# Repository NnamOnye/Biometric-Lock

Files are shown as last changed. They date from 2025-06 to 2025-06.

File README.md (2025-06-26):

ESP-IDF APP
Created by: Nnam Onye
====================

# This is a biometric lock utilizing PIN, and a Finger Print Scanning module.
# This project is already optimized to a certain degree, it can already ask for pin/finger input on first start up + setup
# Has memory to store user pin and finger check and authenticate using memory.
# It can be expanded to save up to as many finger prints and passwords the engineer/designer/user wants.
# The PCB is designed using the same concept as one of my other projects, "keypadPCB" but with additions for the bolt lock,etc..
# I designed the hardware using KiCAD an ECAD Software

# Eclispe Download --> https://eclipseide.org/
# KiCAD Download --> https://www.kicad.org/download/

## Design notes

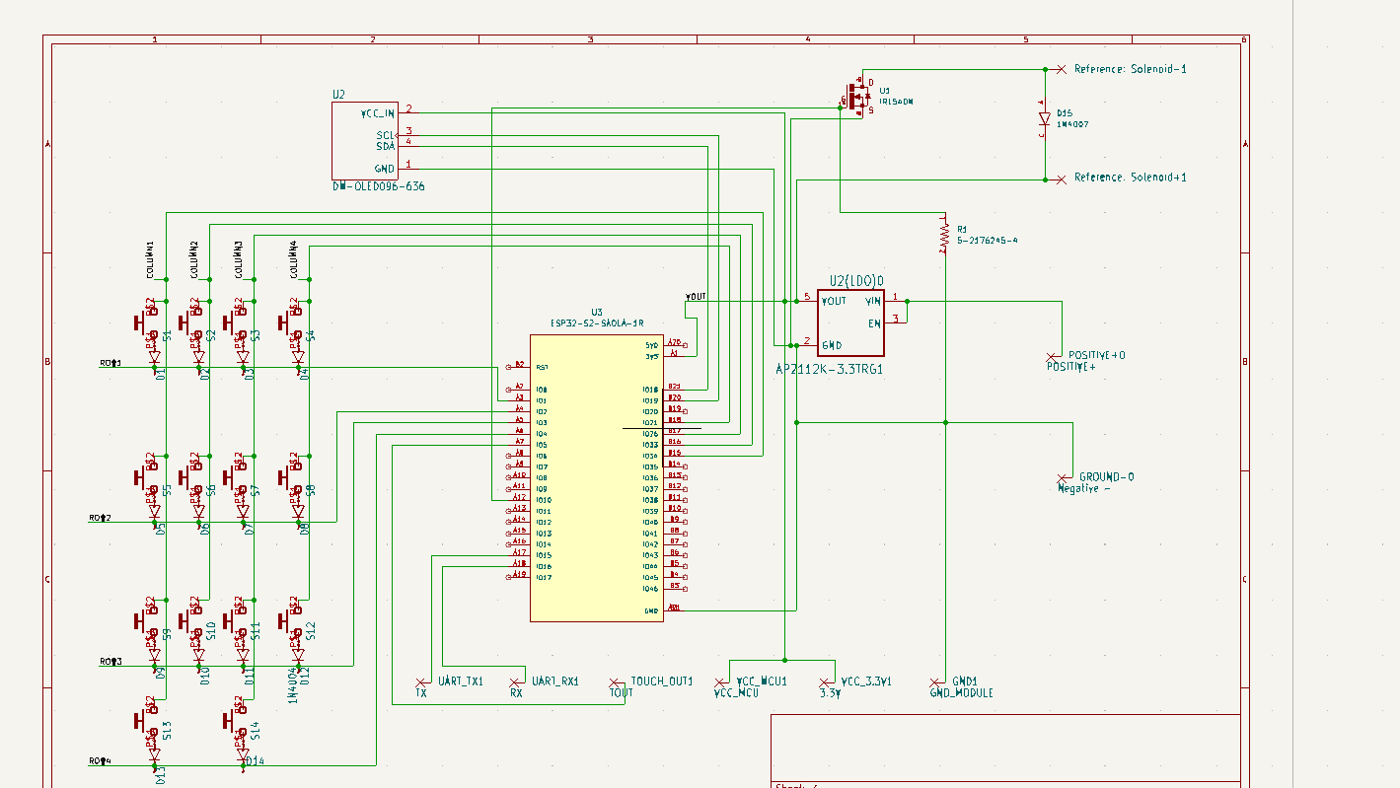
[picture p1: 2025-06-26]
PCB DESIGN/Schematic screenshot.png

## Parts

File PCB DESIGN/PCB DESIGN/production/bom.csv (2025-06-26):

Designator | Footprint | Quantity | Value | LCSC Part #
D1, D10, D11, D12, D13, D14, D2, D3, D4, D5, D6, D7, D8, D9 | DO41-10_210 | 14 | 1N4004
D15 | DIOAD1060W80L520D270 | 1 | 1N4007
GND1 | SMD2,54-5,08_412 | 1 | GND_MODULE
GROUND-0 | SMD2,54-5,08_412 | 1 | Negative -
POSITIVE+0 | SMD2,54-5,08_412 | 1 | POSITIVE+
R1 | RESC3115X65N | 1 | 5-2176245-4
S1, S10, S11, S12, S13, S14, S2, S3, S4, S5, S6, S7, S8, S9 | CHERRY_MX1A-11NN_SWITCH | 14 | MX1A-11NN
SOLENOID+1 | SMD2,54-5,08_412 | 1 | Solenoid+1
SOLENOID-1 | SMD2,54-5,08_412 | 1 | Solenoid-1
TOUCH_OUT1 | SMD2,54-5,08_412 | 1 | TOUT
U1 | TO220V | 1 | IRL540N
U2 | MODULE_DM-OLED096-636 | 1 | DM-OLED096-636
U2(LDO)0 | SOT95P285X140-5N | 1 | AP2112K-3.3TRG1
U3 | XCVR_ESP32-S2-SAOLA-1R | 1 | ESP32-S2-SAOLA-1R
UART_RX1 | SMD2,54-5,08_412 | 1 | RX
UART_TX1 | SMD2,54-5,08_412 | 1 | TX
VCC_3.3V1 | SMD2,54-5,08_412 | 1 | 3.3V
VCC_MCU1 | SMD2,54-5,08_412 | 1 | VCC_MCU

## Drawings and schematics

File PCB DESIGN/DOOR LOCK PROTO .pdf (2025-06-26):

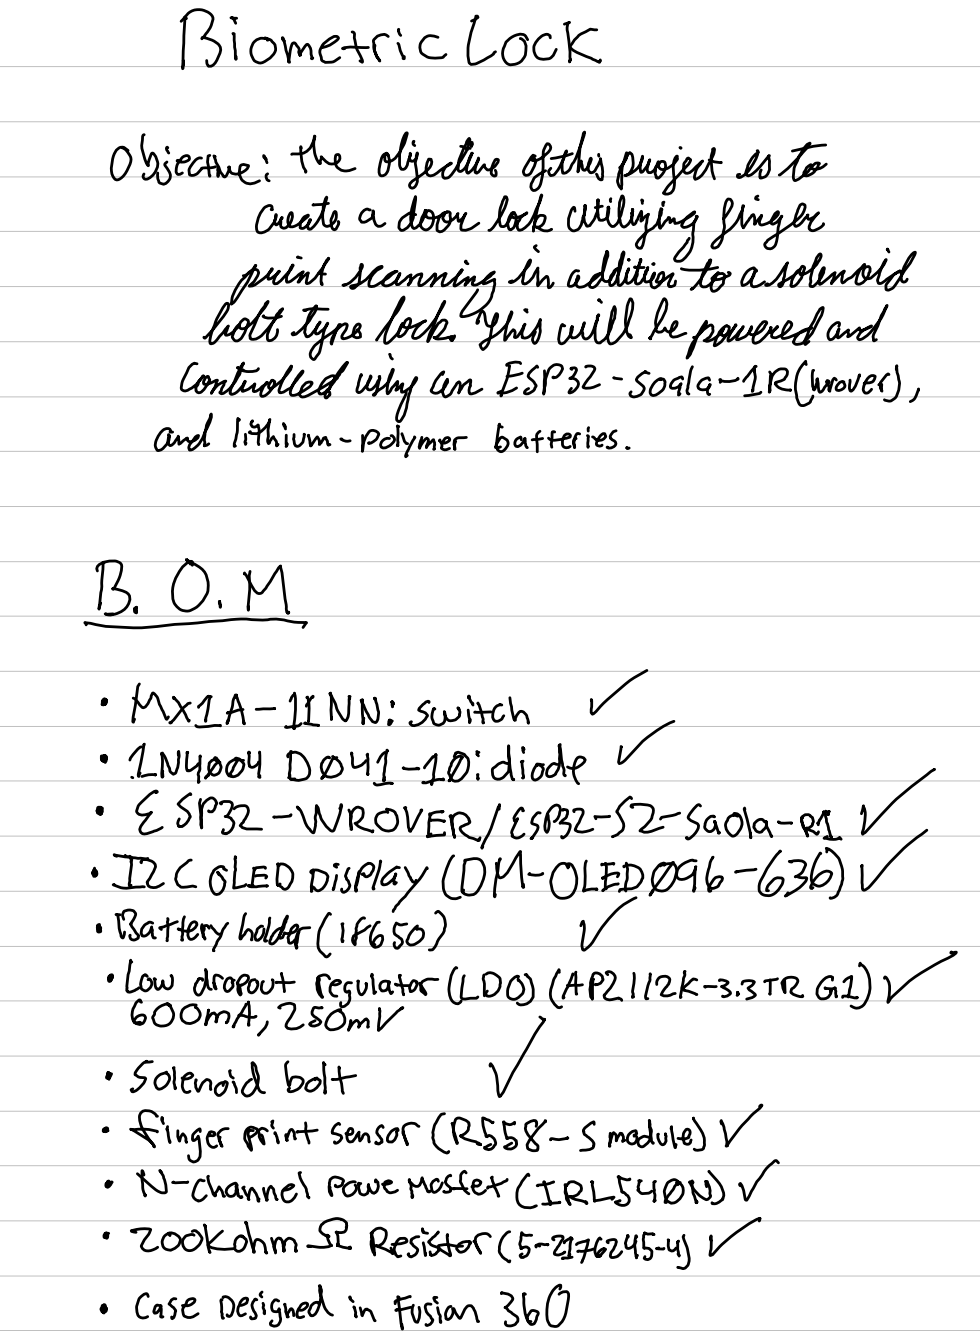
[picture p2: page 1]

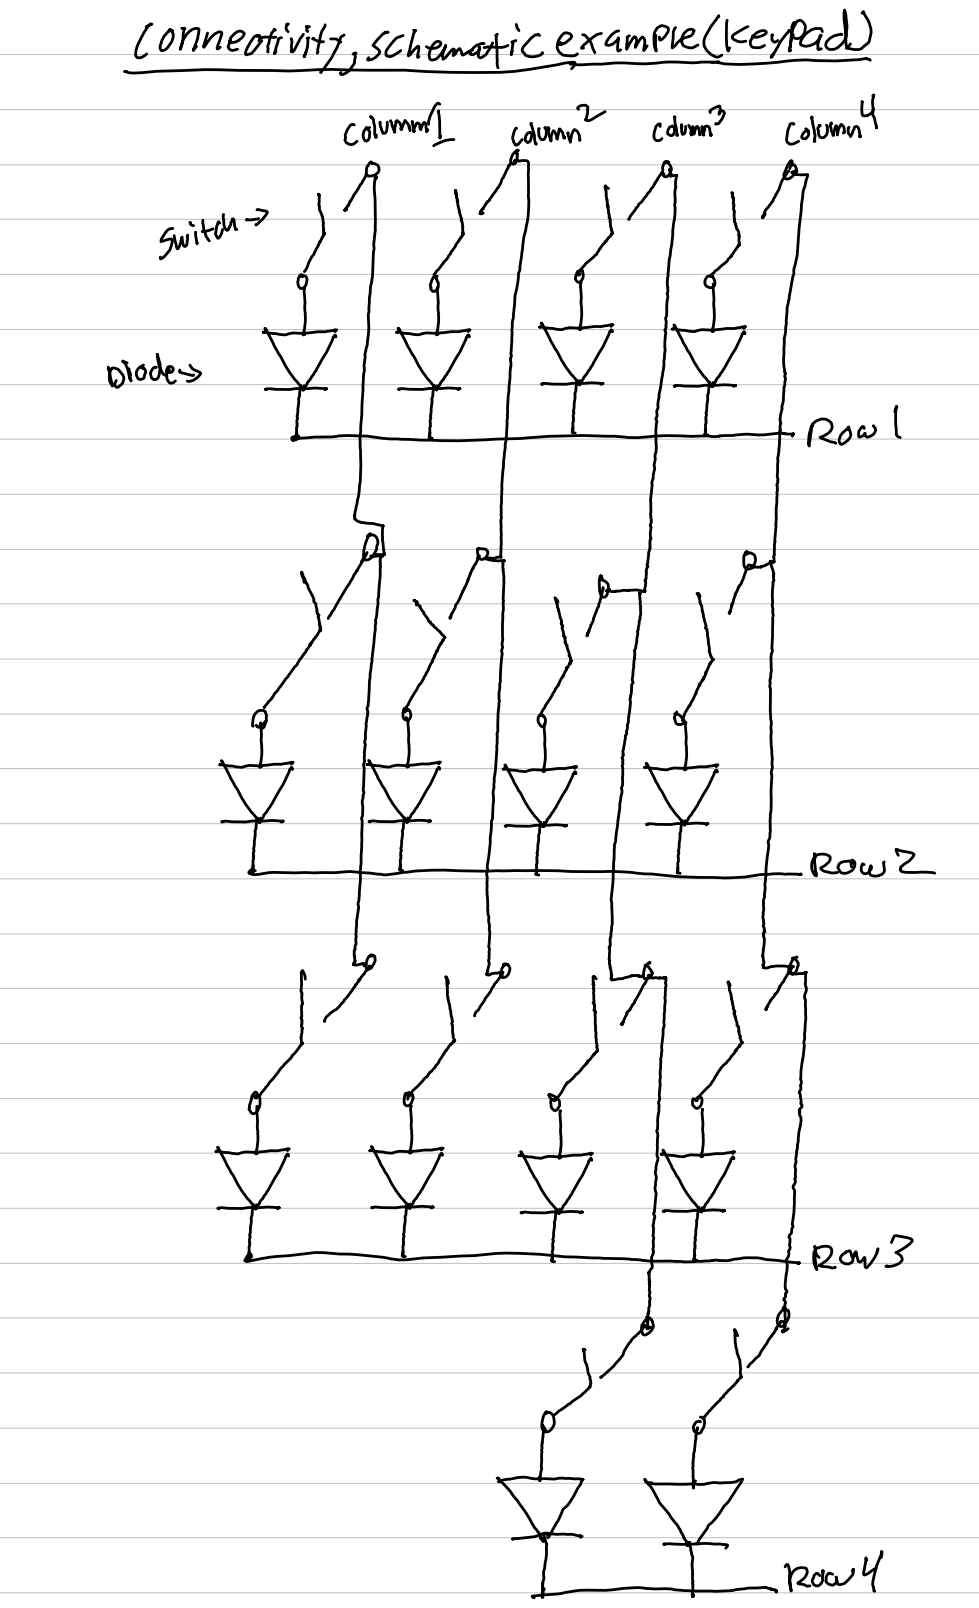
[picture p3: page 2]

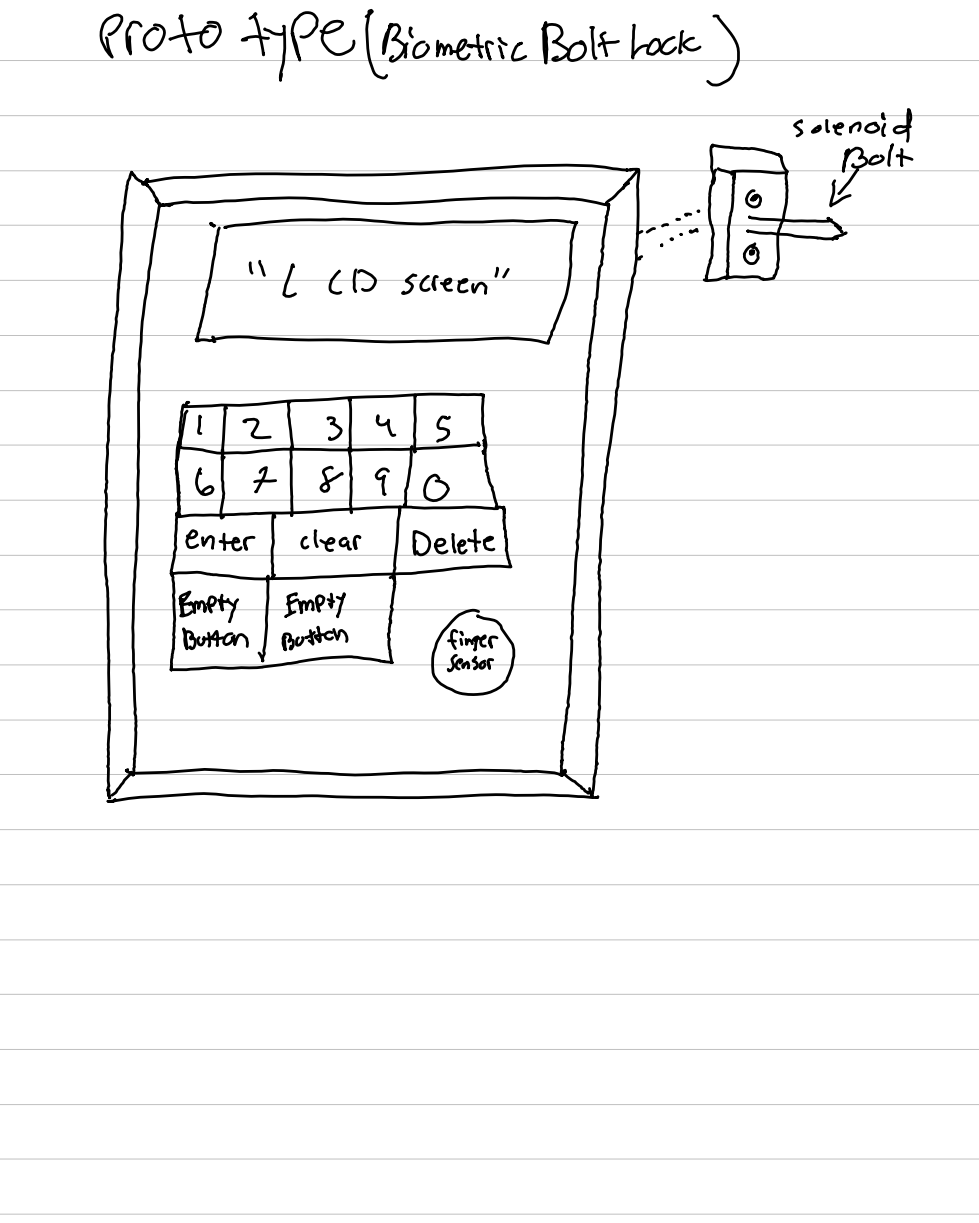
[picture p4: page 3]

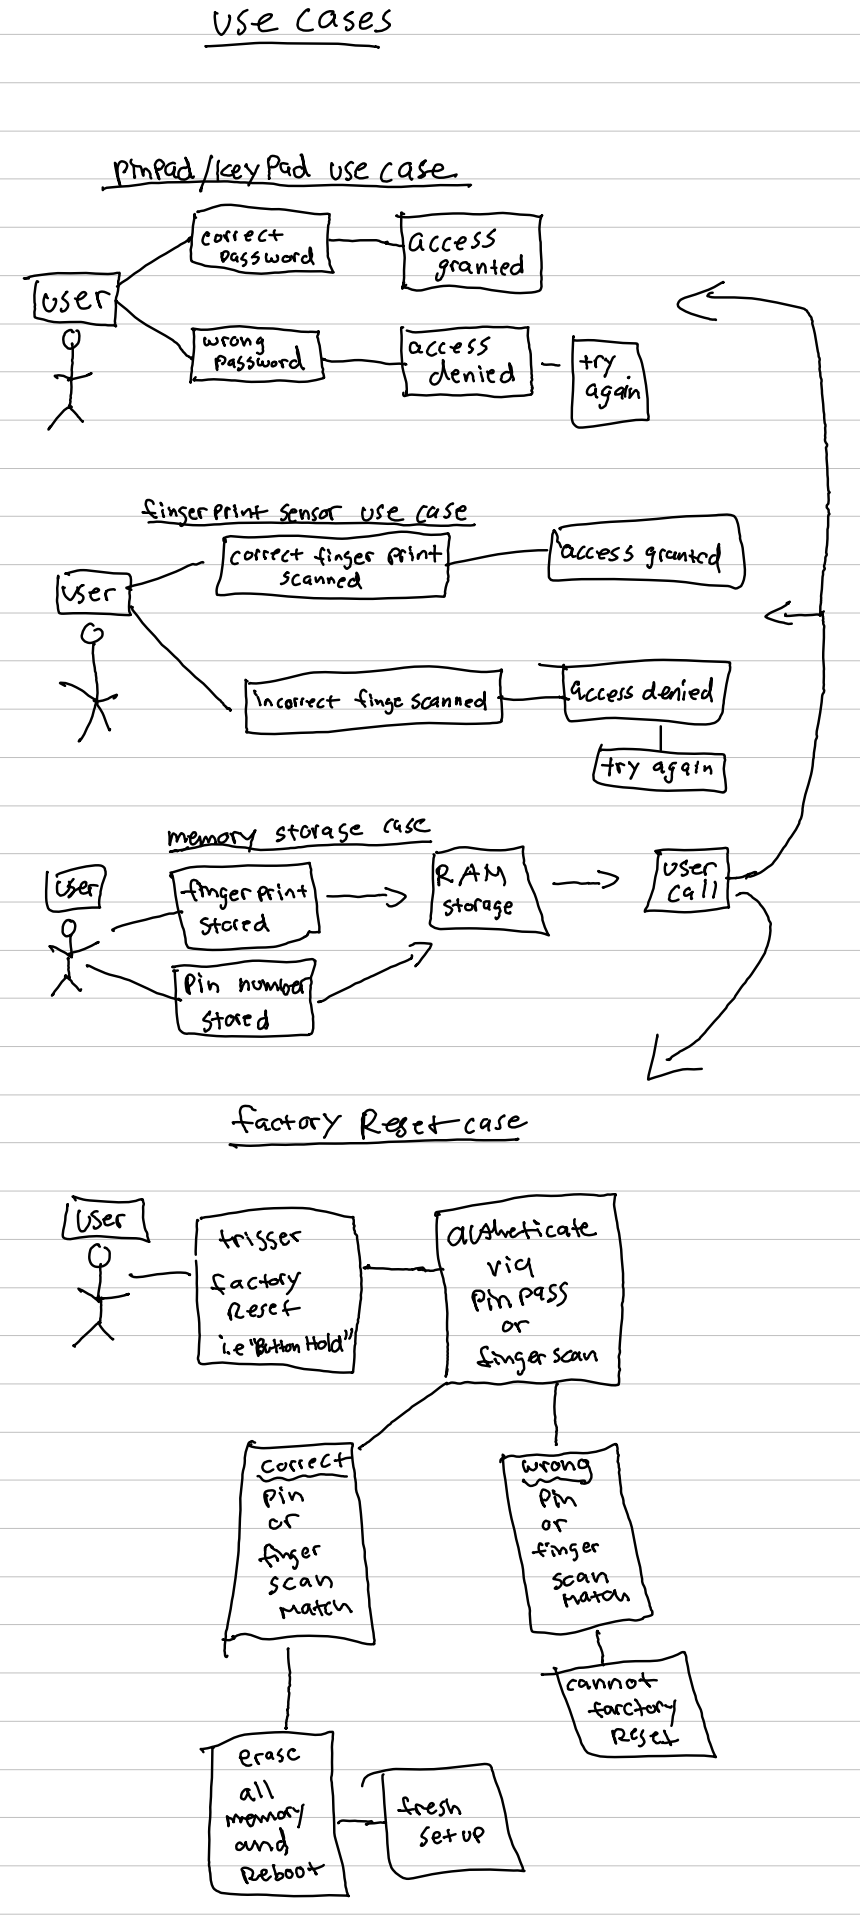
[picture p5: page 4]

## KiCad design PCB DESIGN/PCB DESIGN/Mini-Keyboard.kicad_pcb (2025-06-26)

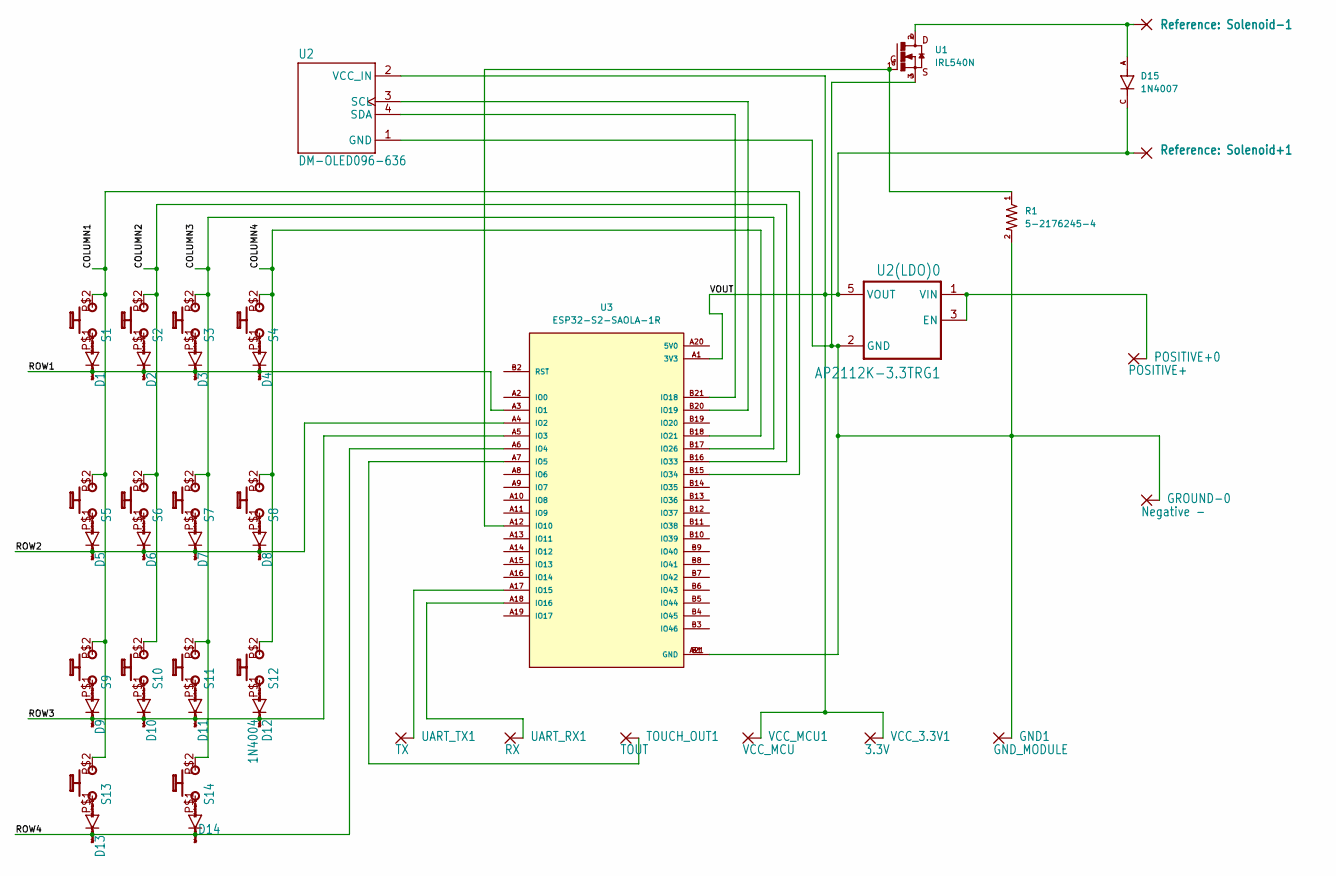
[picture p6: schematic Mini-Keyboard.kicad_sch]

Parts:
D1, D2, D3, D4, D5, D6, D7, D8, D9, D10, D11, D12, D13, D14: 1N4004; DO41-10_210
D15: 1N4007; DIOAD1060W80L520D270; PARTREV G
GND1: GND_MODULE; SMD2,54-5,08_412
GROUND-0: Negative -; SMD2,54-5,08_412
POSITIVE+0: POSITIVE+; SMD2,54-5,08_412
R1: 5-2176245-4; RESC3115X65N
S1, S2, S3, S4, S5, S6, S7, S8, S9, S10, S11, S12, S13, S14: MX1A-11NN; CHERRY_MX1A-11NN_SWITCH
Solenoid+1: Solenoid+1; SMD2,54-5,08_412
Solenoid-1: Solenoid-1; SMD2,54-5,08_412
TOUCH_OUT1: TOUT; SMD2,54-5,08_412
U1: IRL540N; TO220V
U2: DM-OLED096-636; MODULE_DM-OLED096-636
U2(LDO)0: AP2112K-3.3TRG1; SOT95P285X140-5N
U3: ESP32-S2-SAOLA-1R; XCVR_ESP32-S2-SAOLA-1R; PARTREV 1.2
UART_RX1: RX; SMD2,54-5,08_412
UART_TX1: TX; SMD2,54-5,08_412
VCC_3.3V1: 3.3V; SMD2,54-5,08_412
VCC_MCU1: VCC_MCU; SMD2,54-5,08_412

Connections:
/COLUMN1: S1.P$2 (S), S5.P$2 (S), S9.P$2 (S), S13.P$2 (S), U3.B15 (IO34)
/COLUMN2: S2.P$2 (S), S6.P$2 (S), S10.P$2 (S), U3.B16 (IO33)
/COLUMN3: S3.P$2 (S), S7.P$2 (S), S11.P$2 (S), S14.P$2 (S), U3.B17 (IO26)
/COLUMN4: S4.P$2 (S), S8.P$2 (S), S12.P$2 (S), U3.B18 (IO21)
/ROW1: D1.C, D2.C, D3.C, D4.C, U3.A3 (IO1)
/ROW2: D5.C, D6.C, D7.C, D8.C, U3.A4 (IO2)
/ROW3: D9.C, D10.C, D11.C, D12.C, U3.A5 (IO3)
/ROW4: D13.C, D14.C, U3.A6 (IO4)
/VOUT: D15.C, Solenoid+1.1, U2.2 (VCC_IN), U2(LDO)0.5 (VOUT), U3.A1 (3V3), VCC_3.3V1.1, VCC_MCU1.1
unnamed: GND1.1, GROUND-0.1, R1.2, U1.3, U2.1 (GND), U2(LDO)0.2 (GND), U3.A21 (GND), U3.B1 (GND)
unnamed: POSITIVE+0.1, U2(LDO)0.1 (VIN), U2(LDO)0.3 (EN)
unnamed: D1.A, S1.P$1
unnamed: D2.A, S2.P$1
unnamed: D3.A, S3.P$1
unnamed: D4.A, S4.P$1
unnamed: D5.A, S5.P$1
unnamed: D6.A, S6.P$1
unnamed: D7.A, S7.P$1
unnamed: D8.A, S8.P$1
unnamed: D9.A, S9.P$1
unnamed: D10.A, S10.P$1
unnamed: D11.A, S11.P$1
unnamed: D12.A, S12.P$1
unnamed: D13.A, S13.P$1
unnamed: D14.A, S14.P$1
unnamed: D15.A, Solenoid-1.1, U1.2
unnamed: TOUCH_OUT1.1, U3.A7 (IO5)
unnamed: U2.3 (SCL), U3.B20 (IO19)
unnamed: U2.4 (SDA), U3.B21 (IO18)
unnamed: R1.1, U1.1, U3.A12 (IO10)
unnamed: U3.A17 (IO15), UART_TX1.1
unnamed: U3.A18 (IO16), UART_RX1.1

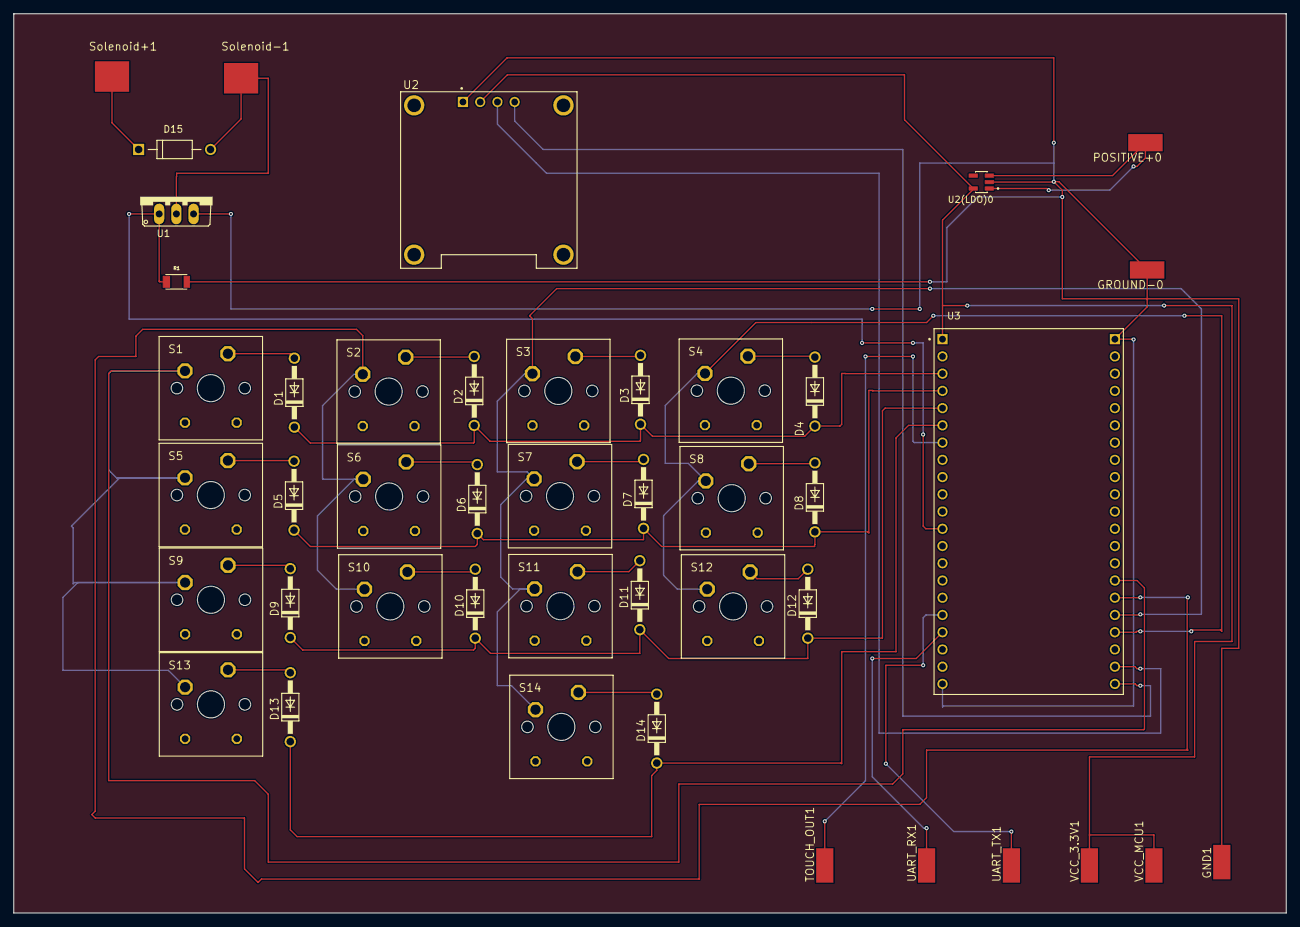
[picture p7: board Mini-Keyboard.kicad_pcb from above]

Board: 2 copper layers, 187.5 x 132.5 mm, 44 parts (0 on the bottom side), 32 nets.

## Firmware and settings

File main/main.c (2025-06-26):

#include <stdio.h>
#include <stdbool.h>
#include <unistd.h>
#include"buttonsource.h"
#include "esp_log.h"
#include"fingersource.h"
#include "freertos/idf_additions.h"
#include "ssd1306.h"
#include<driver/gpio.h>
#include "nvs_flash.h"

void app_main(void)
{
	// Initialize NVS (required for saving password/finger print config)
    esp_err_t ret = nvs_flash_init();
    if (ret == ESP_ERR_NVS_NO_FREE_PAGES || ret == ESP_ERR_NVS_NEW_VERSION_FOUND) {
        nvs_flash_erase();
        nvs_flash_init();
    }
	
	char input_buffer[32] = {0};
	screen_on();
	check_for_savedpass(input_buffer, sizeof(input_buffer)); // this function checks for save pass and if none save it will prompt for creation. In that event its acting as a first time setup function also.
	init_fingerprint_uart();
	run_first_time_setup();
	fpm_check_library_contains(8);
	check_fingerprint_match();
	try_factory_reset();
	fpm_sleep();
	power_manager();
	
	static TickType_t last_fingerprint_time = 0;
	TickType_t now = xTaskGetTickCount();
	
	while (true) {
    	
    	scan_keypad();
    	
    	handle_key_action(-1);
    	
	    // === 2. Check Fingerprint Sensor ===
	    if (gpio_get_level(TOUCHOUT_GPIO) == 0) {  // defined in fingersource.c
	    	check_fingerprint_match();
	    	/*if (check_fingerprint_match() && (now - last_fingerprint_time > pdMS_TO_TICKS(3000))) {
	    		unlock_solenoid();
	    		last_fingerprint_time = now;
			}*/ //---> uncomment this if statement if the lock repeatedly unlocks after access granted with finger print
	        //ESP_LOGE("AUTH", "Fingerprint access granted!");
	    }
	
	    // === 3. Small delay for polling stability ===
	    vTaskDelay(pdMS_TO_TICKS(100));  // ~100ms loop
	}
}

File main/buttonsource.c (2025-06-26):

/*
 * buttonsource.c
 *
 *  Created on: Apr 3, 2025
 *      Author: M.O
 */
//#include<stdio.h>
#include<driver/gpio.h>
//#include "driver/i2c.h"
#include "esp_sleep.h"
#include "soc/gpio_num.h"
#include "ssd1306.h"
#include <stdbool.h>
#include <stdio.h>
#include <string.h>
#include "driver/uart.h"
#include<esp_log.h>
//#include "i2c_master.h"
#include"driver/i2c_master.h"
#include "nvs.h"
#include "nvs_flash.h"
#include <stdio.h>
#include"fingersource.h"

#define ESP_LOGI(tag, format, ...)
#define ESP_LOGE(tag, format, ...)

#define NVS_NAMESPACE "storage"
#define NVS_KEY_PASSWORD "password"

#define CONFIG_OFFSETX 0  // or 2, or whatever the offset needs to be



//defining the prototypes bellow since some functions call functions that have not been declared yet at the time of specified function call you can reorganize if you like
void run_first_time_setup(void);
void get_password_input(char *buffer);
esp_err_t save_password(const char *password);
void check_entered_password(const char *input);
void check_for_savedpass(char *buffer, size_t buffer_len);
void handle_key_action(int key);
void scan_keypad();


void screen_on() 
{
    
    // Initialize the OLED display
    SSD1306_t dev;  // Define the SSD1306 display instance
    
    i2c_master_init(&dev, /*sda_gpio*/18 ,/*scl_gpio*/19,/*reset_gpio*/ -1);
    ssd1306_init(&dev, 126, 64); // Correct initialization

    // Clear the screen and display text
    ssd1306_clear_screen(&dev, false);
    ssd1306_display_text(&dev,2, "Hello!",6,false);  // Pass device handle and coordinates
    vTaskDelay(pdMS_TO_TICKS(4000));  // Wait 4 second
    ssd1306_clear_screen(&dev, false);
}

// Define row GPIO pins
#define ROW1_GPIO GPIO_NUM_1
#define ROW2_GPIO GPIO_NUM_2
#define ROW3_GPIO GPIO_NUM_3
#define ROW4_GPIO GPIO_NUM_4


// Define column GPIO pins
#define COL1_GPIO GPIO_NUM_34
#define COL2_GPIO GPIO_NUM_33
#define COL3_GPIO GPIO_NUM_26
#define COL4_GPIO GPIO_NUM_21


//Solenoid Bolt-->MOSFET GPIO Pin
#define BOLT_MOSFET_GPIO GPIO_NUM_10

//Long press for Clear button
#define LONG_PRESS_TIME_MS 2500  // Define long press time in ms

//Long press for RESET button
#define LONG_PRESS_RESET_MS 10000   // Define long press time in ms for reset

//Long press for factory reset
#define LONG_PRESS_FACTORY_RESET_MS 40000 // Define long press time in ms for factory reset


void configure_buttons() {
	//Row Configuration
    gpio_config_t row1_conf = {
    .pin_bit_mask = (1ULL << ROW1_GPIO),
    .mode = GPIO_MODE_INPUT,
    .pull_up_en = GPIO_PULLUP_ENABLE,
    .intr_type = GPIO_INTR_DISABLE
	};
	
	gpio_config_t row2_conf = {
	    .pin_bit_mask = (1ULL << ROW2_GPIO),
	    .mode = GPIO_MODE_INPUT,
	    .pull_up_en = GPIO_PULLUP_ENABLE,
	    .intr_type = GPIO_INTR_DISABLE
	};
	
	gpio_config_t row3_conf = {
	    .pin_bit_mask = (1ULL << ROW3_GPIO),
	    .mode = GPIO_MODE_INPUT,
	    .pull_up_en = GPIO_PULLUP_ENABLE,
	    .intr_type = GPIO_INTR_DISABLE
	};
	
	gpio_config_t row4_conf = {
	    .pin_bit_mask = (1ULL << ROW4_GPIO),
	    .mode = GPIO_MODE_INPUT,
	    .pull_up_en = GPIO_PULLUP_ENABLE,
	    .intr_type = GPIO_INTR_DISABLE
	};
	
	// Column configuration
	gpio_config_t col1_conf = {
	    .pin_bit_mask = (1ULL << COL1_GPIO),
	    .mode = GPIO_MODE_OUTPUT,
	    .pull_up_en = GPIO_PULLUP_DISABLE,
	    .intr_type = GPIO_INTR_DISABLE
	};
	
	gpio_config_t col2_conf = {
	    .pin_bit_mask = (1ULL << COL2_GPIO),
	    .mode = GPIO_MODE_OUTPUT,
	    .pull_up_en = GPIO_PULLUP_DISABLE,
	    .intr_type = GPIO_INTR_DISABLE
	};
	
	gpio_config_t col3_conf = {
	    .pin_bit_mask = (1ULL << COL3_GPIO),
	    .mode = GPIO_MODE_OUTPUT,
	    .pull_up_en = GPIO_PULLUP_DISABLE,
	    .intr_type = GPIO_INTR_DISABLE
	};
	
	gpio_config_t col4_conf = {
	    .pin_bit_mask = (1ULL << COL4_GPIO),
	    .mode = GPIO_MODE_OUTPUT,
	    .pull_up_en = GPIO_PULLUP_DISABLE,
	    .intr_type = GPIO_INTR_DISABLE
	};
	
	
	
	//SOLENOID BOLT--> MOSFET CONFIGURATION
	gpio_config_t mosfet_conf = {
	    .pin_bit_mask = (1ULL << BOLT_MOSFET_GPIO),
	    .mode = GPIO_MODE_INPUT,
	    .pull_up_en = GPIO_PULLUP_DISABLE,
	    .intr_type = GPIO_INTR_POSEDGE
	};
	gpio_set_level(BOLT_MOSFET_GPIO, 0);
	
    
    //Row pin GPIO CONFIG
    gpio_config(&row1_conf);
    gpio_config(&row2_conf);
    gpio_config(&row3_conf);
    gpio_config(&row4_conf);
    
    
    //Column pin GPIO CONFIG
    gpio_config(&col1_conf);
	gpio_config(&col2_conf);
	gpio_config(&col3_conf);
	gpio_config(&col4_conf);
    
    
    //Bolt --> Mosfet configuration
    gpio_config(&mosfet_conf);
    
}



esp_err_t save_password(const char *password) {  
    nvs_handle_t nvs;
    esp_err_t err = nvs_open("storage", NVS_READWRITE, &nvs);
    if (err != ESP_OK) return err;

    err = nvs_set_str(nvs, "password", password);
    if (err == ESP_OK) {
        err = nvs_commit(nvs);
    }
    nvs_close(nvs);
    return err;
}

esp_err_t load_password(char *buffer, size_t len) {
    nvs_handle_t nvs_handle;
    esp_err_t err = nvs_open(NVS_NAMESPACE, NVS_READONLY, &nvs_handle);
    if (err != ESP_OK) {
        ESP_LOGE("NVS", "Failed to open NVS: %s", esp_err_to_name(err));
        return err;
    }

    size_t required_size = len;
    err = nvs_get_str(nvs_handle, NVS_KEY_PASSWORD, buffer, &required_size);
    if (err == ESP_OK) {
        ESP_LOGI("NVS", "Password loaded: %s", buffer);
    } else if (err == ESP_ERR_NVS_NOT_FOUND) {
        ESP_LOGW("NVS", "Password not found in NVS.");
    } else {
        ESP_LOGE("NVS", "Error reading password: %s", esp_err_to_name(err));
    }

    nvs_close(nvs_handle);
    return err;
}


void run_first_time_setup() { // call this function in main only if neccesary or if needed
	 char input_buffer[32] = {0};
     SSD1306_t dev;
     const int max_attempts = 3;
     int attempts = 0;
     
     while (attempts < max_attempts) {
		
		ssd1306_clear_screen(&dev, false);
    	ssd1306_display_text(&dev, 2, "Set Password", 12, false);
    	vTaskDelay(pdMS_TO_TICKS(1000));

    	get_password_input(input_buffer);  // blocks until password entered
    	save_password(input_buffer);

    	if (save_password(input_buffer) == ESP_OK) {
        	ESP_LOGI("SETUP", "Password set.");
        	ssd1306_display_text(&dev, 4, "Password Created", 14, false);
        	vTaskDelay(pdMS_TO_TICKS(3000));
        	
    	} else {
        	ESP_LOGE("SETUP", "Failed to set password/Finger Scan.");
        	ssd1306_display_text(&dev, 4, "Save Failed.", 11, false);
        	vTaskDelay(pdMS_TO_TICKS(4000));
        	
    	}
	 }
	 setup_new_fingerprint();// set outside of attempt loop because if user cannot set pass they can set finger print to factory reset.
	 
	 attempts++; //IF SETUP FAILS, USER WILL HAVE ONLY 3 TRIES TO SETUP

    
}
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
